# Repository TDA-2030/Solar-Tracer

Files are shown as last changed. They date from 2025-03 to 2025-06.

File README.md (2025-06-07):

# 太阳追踪器

## 参考

- https://www.pveducation.org/zh-hans/pvcdrom/%E9%98%B3%E5%85%89%E7%9A%84%E5%B1%9E%E6%80%A7/%E5%A4%AA%E9%98%B3%E7%9A%84%E9%AB%98%E7%B2%BE%E5%BA%A6%E5%AE%9A%E4%BD%8D
- http://106.37.81.211:8082/images/sjsimages/pdf/xw/xwB215_hebing/Y2177876.pdf
- https://jonacappelle.github.io/Master-Thesis/_madgwick_a_h_r_s_8c.html
- https://gml.noaa.gov/grad/solcalc/
- https://zh.planetcalc.com/318/

## 编译

esp-idf 版本：8497af9b77

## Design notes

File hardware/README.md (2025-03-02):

# Ferris Wheel

```
 ________                          __                 __       __ __                         __ 
|        \                        |  \               |  \  _  |  |  \                       |  \
| $$$$$$$______   ______   ______  \$$ _______       | $$ / \ | $| $$____   ______   ______ | $$
| $$__  /      \ /      \ /      \|  \/       \      | $$/  $\| $| $$    \ /      \ /      \| $$
| $$  \|  $$$$$$|  $$$$$$|  $$$$$$| $|  $$$$$$$      | $$  $$$\ $| $$$$$$$|  $$$$$$|  $$$$$$| $$
| $$$$$| $$    $| $$   \$| $$   \$| $$\$$    \       | $$ $$\$$\$| $$  | $| $$    $| $$    $| $$
| $$   | $$$$$$$| $$     | $$     | $$_\$$$$$$\      | $$$$  \$$$| $$  | $| $$$$$$$| $$$$$$$| $$
| $$    \$$     | $$     | $$     | $|       $$      | $$$    \$$| $$  | $$\$$     \\$$     | $$
 \$$     \$$$$$$$\$$      \$$      \$$\$$$$$$$        \$$      \$$\$$   \$$ \$$$$$$$ \$$$$$$$\$$
                                                                                                         
```

~ 一座点缀着繁星般灯光的旋转梦想摩天轮。🌟🎡 ~



## 使用说明

1. 插入电源，等待亮灯，在联网和不联网状态下都会在几秒后进入灯效循环播放，直到收到新的灯效指令。
2. 根据灯的颜色指示，判断当前状态
   1. 亮**红色**说明没有未配置网络，需要按照 `步骤 3` 进行配置
   2. 亮**紫色**说明已经配网，正在连接，只需等待连接完成变成**淡蓝色**即可

3. 配网步骤：
   1. 打开 RainMaker APP 
   2. 点击`添加设备`按钮
   3. 扫描下面的二维码   
   
4. 选择想要连接的 WiFi
5. 输入对应 WiFi 的密码
6. 点击`开始`按钮

## 硬件说明

- 供电输入：12V - 2A
- LED 灯数量：208 * 2
- 摩天轮坐舱数量：16
- 模型比例：1:100

## 灯颜色指示
1. 亮红色：未配网，等待配网
2. 亮紫色：正在联网
3. 亮蓝色：已联网，等待连接云端
4. 亮淡蓝色：已连接云端，可正常使用

## 重置设备方法

当你需要换一个 WiFi 连接或者不要联网的时候需要重置设备。

方法：插上电源等待亮灯一秒后拔掉电源，熄灭后再次插上电源，再次等待亮灯一秒后拔掉电源，如此**反复5次**后插上电源不再拔掉等待灯变成红色即重置成功。

## 编译固件的说明

下载 [ESP-IDF](https://github.com/espressif/esp-idf)，并安装好 ESP-IDF

> 库版本说明：
>
> esp-rainmaker: 7d506420d320a137bce6aaeb69a2059cc162efac
> esp-idf: 97bf63addecd1857a7017a29823a6c70fec99b04

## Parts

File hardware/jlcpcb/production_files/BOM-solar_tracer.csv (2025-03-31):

Comment | Designator | Footprint | LCSC
BMI270 | U3 | LGA-14_L3.0-W2.5-P0.50-BR | C2836813
QMC5883L | U4 | LGA-16_L3.0-W3.0-P0.50-BL_SQ | C976032
MountingHole_Pad | H4 | MountingHole_3.2mm_M3_Pad_Via
MountingHole_Pad | H1 | MountingHole_3.2mm_M3_Pad_Via
10uf | C10 | C_0603
10uf | C9 | C_0603
10uf | C7 | C_1206_3216Metric
10uf | C2 | C_0603
AT8236 | U6 | SOIC-8-1EP_3.9x4.9mm_P1.27mm_EP2.29x3mm
AT8236 | U5 | SOIC-8-1EP_3.9x4.9mm_P1.27mm_EP2.29x3mm
TX4137 | U2 | SOT-23-6
ESP32-S3-WROOM-1 | U1 | ESP32-S3-WROOM-1
0R | R15 | R_0402
0R | R14 | R_0402
4.7k | R13 | R_0402
4.7k | R12 | R_0402
NC | R11 | R_0402
NC | R10 | R_0402
1k | R9 | R_0402
10k | R8 | R_0402
10k | R7 | R_0402
100k | R6 | R_0402
33k | R5 | R_0402
200k | R4 | R_0402
4.7k | R3 | R_0402
4.7k | R2 | R_0402
10k | R1 | R_0402
22uH | L1 | L_Taiyo-Yuden_NR-40xx
MOTX | J7 | PinHeader_1x02_P2.54mm_Vertical
MOTX_ENCODER | J6 | PinHeader_1x04_P2.54mm_Vertical
MOTY | J5 | PinHeader_1x02_P2.54mm_Vertical
MOTY_ENCODER | J4 | PinHeader_1x04_P2.54mm_Vertical
POWER | J3 | PinHeader_1x02_P2.54mm_Vertical
GPS | J2 | PinHeader_1x04_P2.54mm_Vertical
DEBUG | J1 | PinHeader_1x06_P2.54mm_Vertical
MountingHole_Pad | H3 | MountingHole_3.2mm_M3_Pad_Via
MountingHole_Pad | H2 | MountingHole_3.2mm_M3_Pad_Via
RED | D5 | LED_0603
SMF5V0A | D4 | D_SMF
B5819W SL | D3 | D_SOD-123
RED | D2 | LED_0603
GREEN | D1 | LED_0603
10uf | C20 | C_0603
10uf | C19 | C_0603
100nf | C18 | C_0402
100nf | C17 | C_0402
4.7uf | C16 | C_0402
100nf | C15 | C_0402
220nf | C14 | C_0402
100nf | C13 | C_0402
100nf | C12 | C_0402
100n | C11 | C_0402
10uf | C8 | C_1206_3216Metric
10uf | C6 | C_1206_3216Metric
10uf | C5 | C_1206_3216Metric
100nf | C4 | C_0402
100nf | C3 | C_0402
100nf | C1 | C_0402

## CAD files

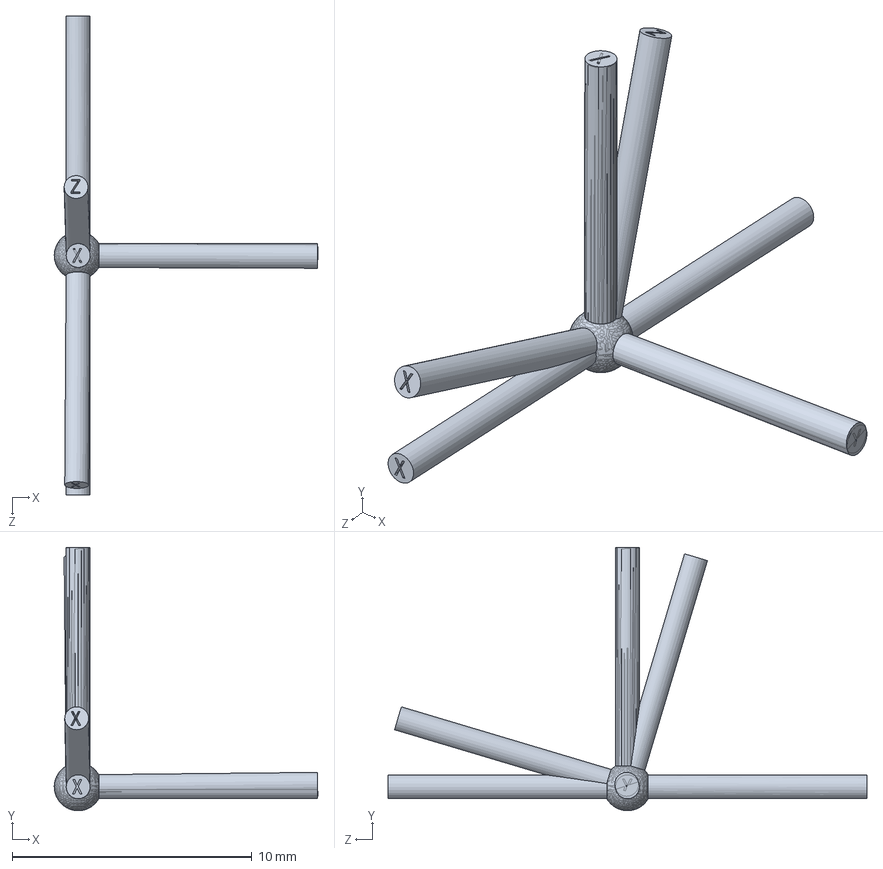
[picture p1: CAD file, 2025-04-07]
3d/坐标系.SLDASM
11.0 x 11.0 x 20.0 mm
坐标系 x 3

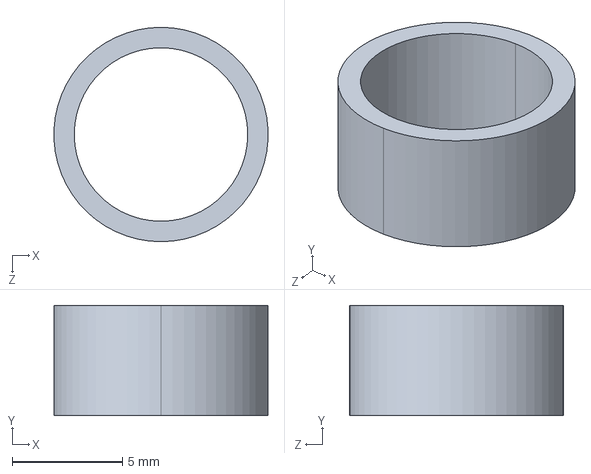
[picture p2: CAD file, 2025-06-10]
3d/轴套.STEP
9.69 x 5.00 x 9.70 mm

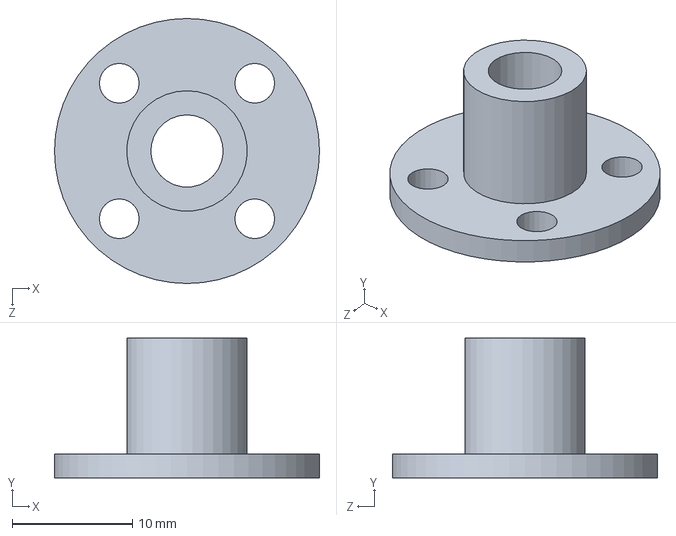
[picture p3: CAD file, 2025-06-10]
3d/法兰.SLDPRT
22.0 x 11.6 x 22.0 mm

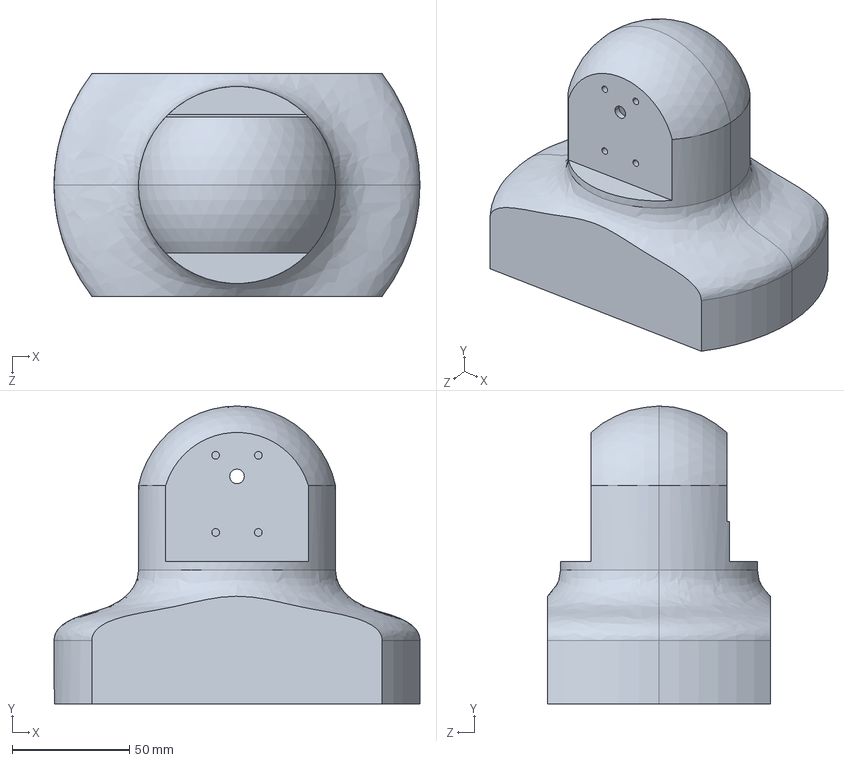
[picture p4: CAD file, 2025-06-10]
3d/上壳.STEP
156.0 x 127.0 x 95.0 mm

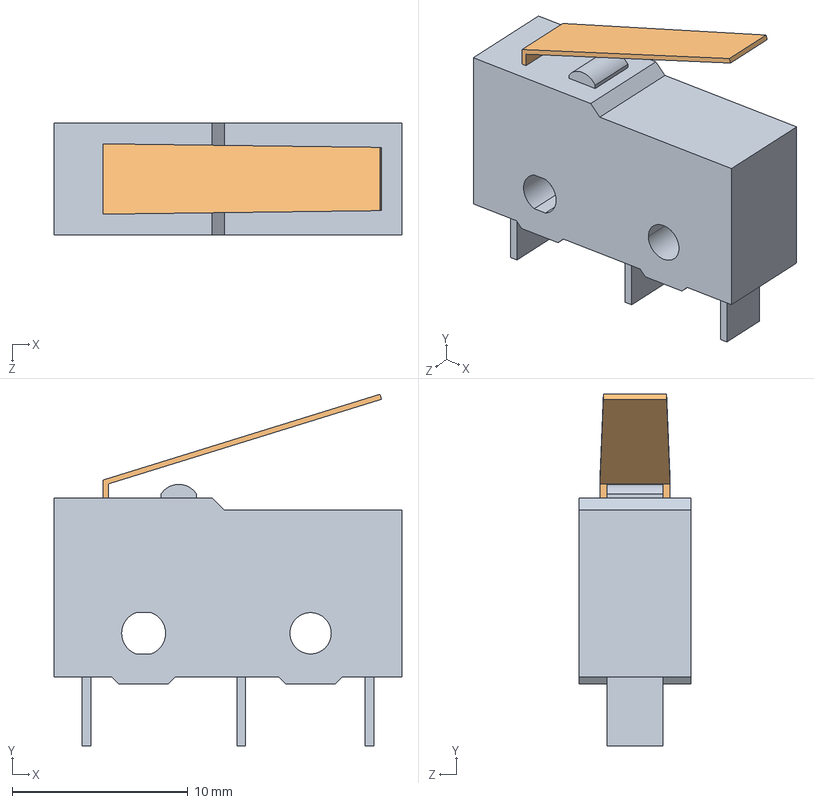
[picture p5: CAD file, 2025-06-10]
3d/SS_01GL_E.step
19.8 x 20.0 x 6.40 mm
SS_01GL_E_BASE
SS_01GL_E_ACTUATOR

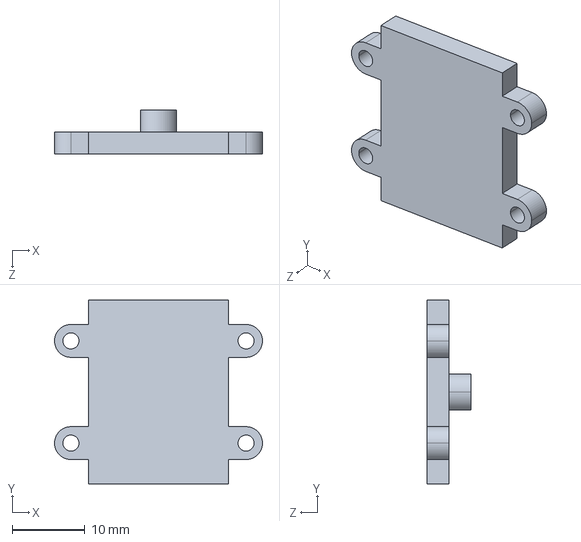
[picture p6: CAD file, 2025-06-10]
3d/imu盖板.STEP
28.5 x 25.2 x 6.00 mm

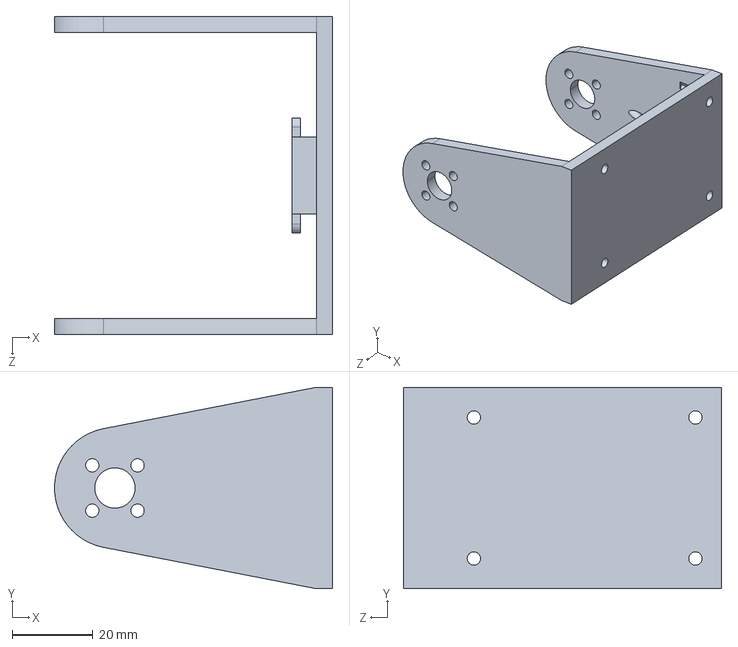
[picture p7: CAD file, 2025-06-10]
3d/U型板.STEP
69.0 x 50.0 x 79.0 mm

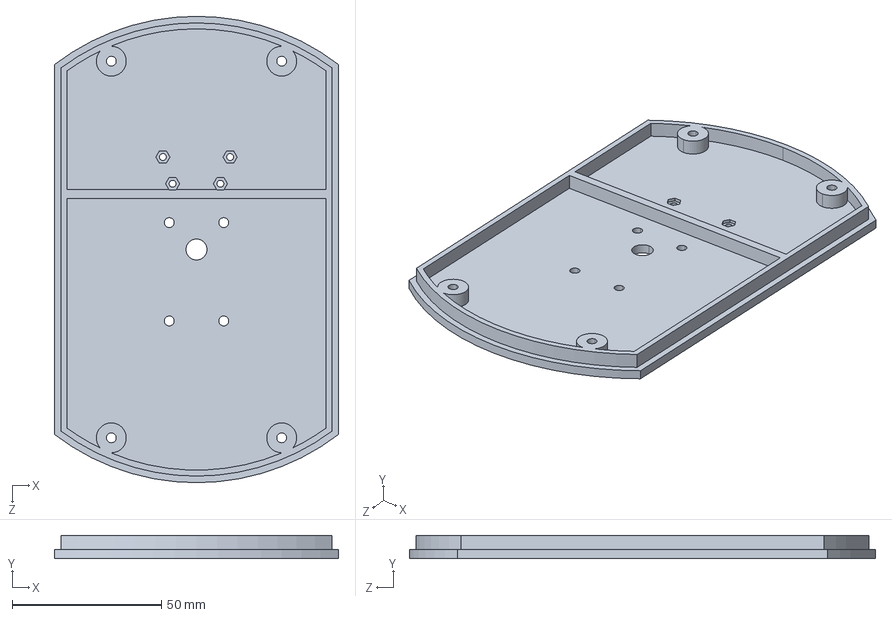
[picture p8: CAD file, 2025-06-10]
3d/底板.STEP
95.0 x 7.80 x 156.0 mm

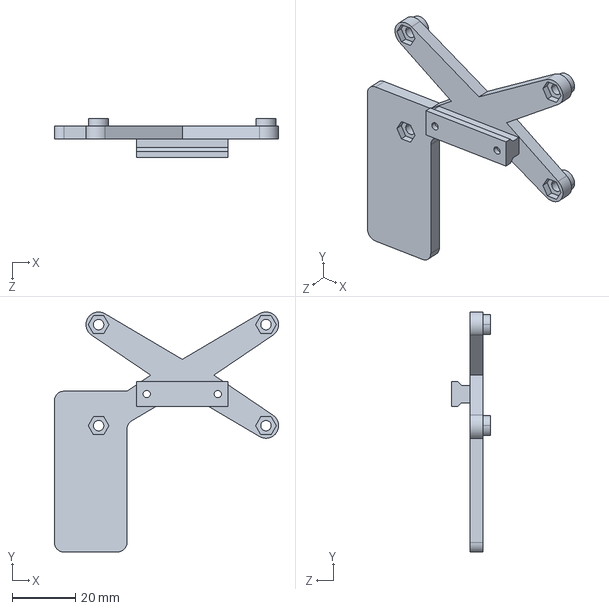
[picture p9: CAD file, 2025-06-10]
3d/pcb支架.STEP
71.0 x 76.0 x 12.5 mm

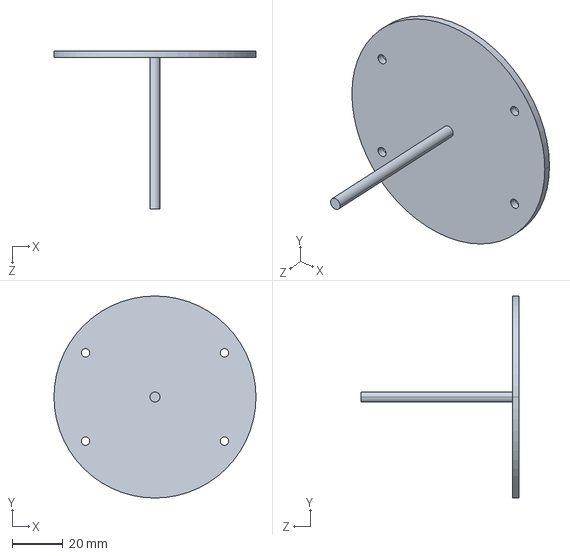
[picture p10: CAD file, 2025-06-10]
3d/太阳指向盘.STEP
80.0 x 80.0 x 62.5 mm

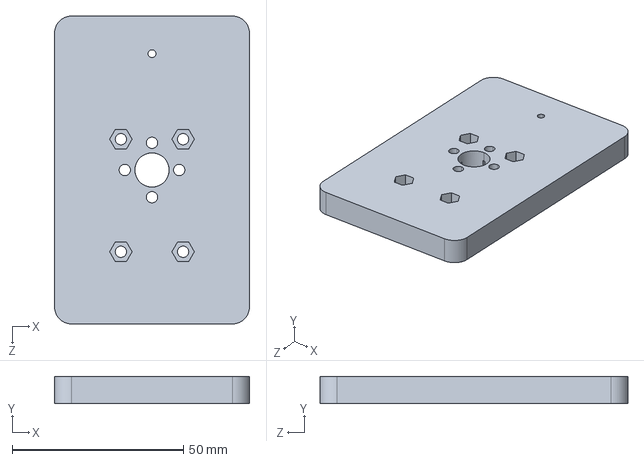
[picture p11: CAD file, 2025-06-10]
3d/底座.STEP
57.0 x 8.00 x 90.0 mm

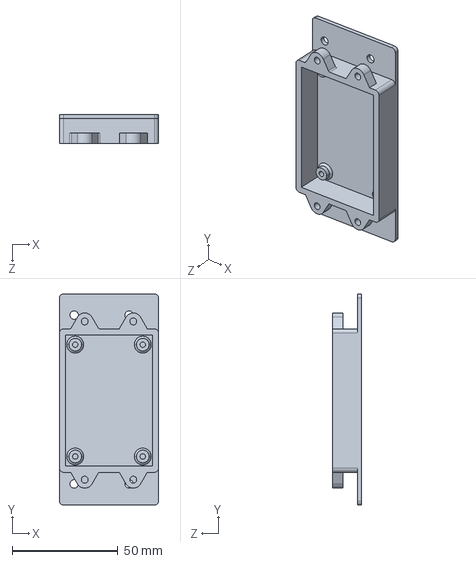
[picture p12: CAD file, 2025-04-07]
3d/imu固定板.STEP
47.0 x 100.0 x 13.8 mm

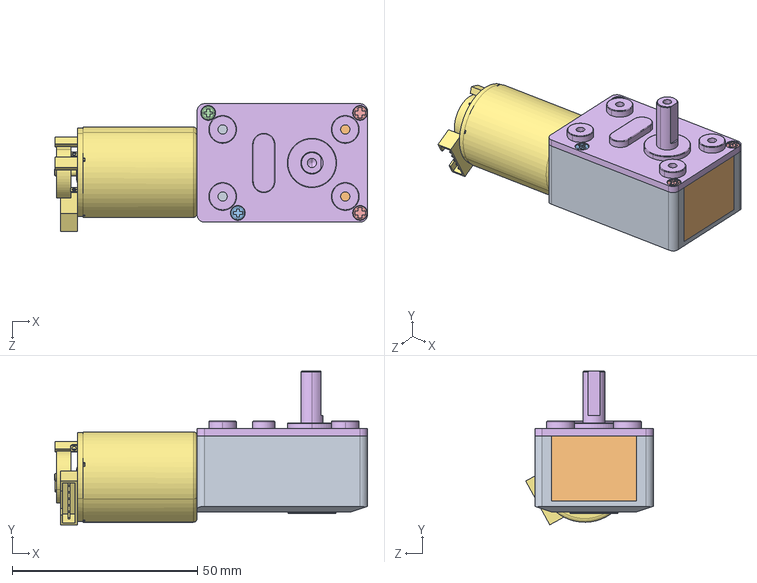
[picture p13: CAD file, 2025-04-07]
3d/2814300907JGY-370编码器.STEP
84.5 x 41.5 x 34.5 mm
JGY-370 -636
370晤鎢ん

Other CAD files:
3d/U型板.SLDPRT
3d/imu固定板.SLDPRT
3d/imu盖板.SLDPRT
3d/pcb支架.SLDPRT
3d/上壳.SLDPRT
3d/坐标系.SLDPRT
3d/太阳指向盘.SLDPRT
3d/底座.SLDPRT
3d/底板.SLDPRT
3d/轴套.SLDPRT

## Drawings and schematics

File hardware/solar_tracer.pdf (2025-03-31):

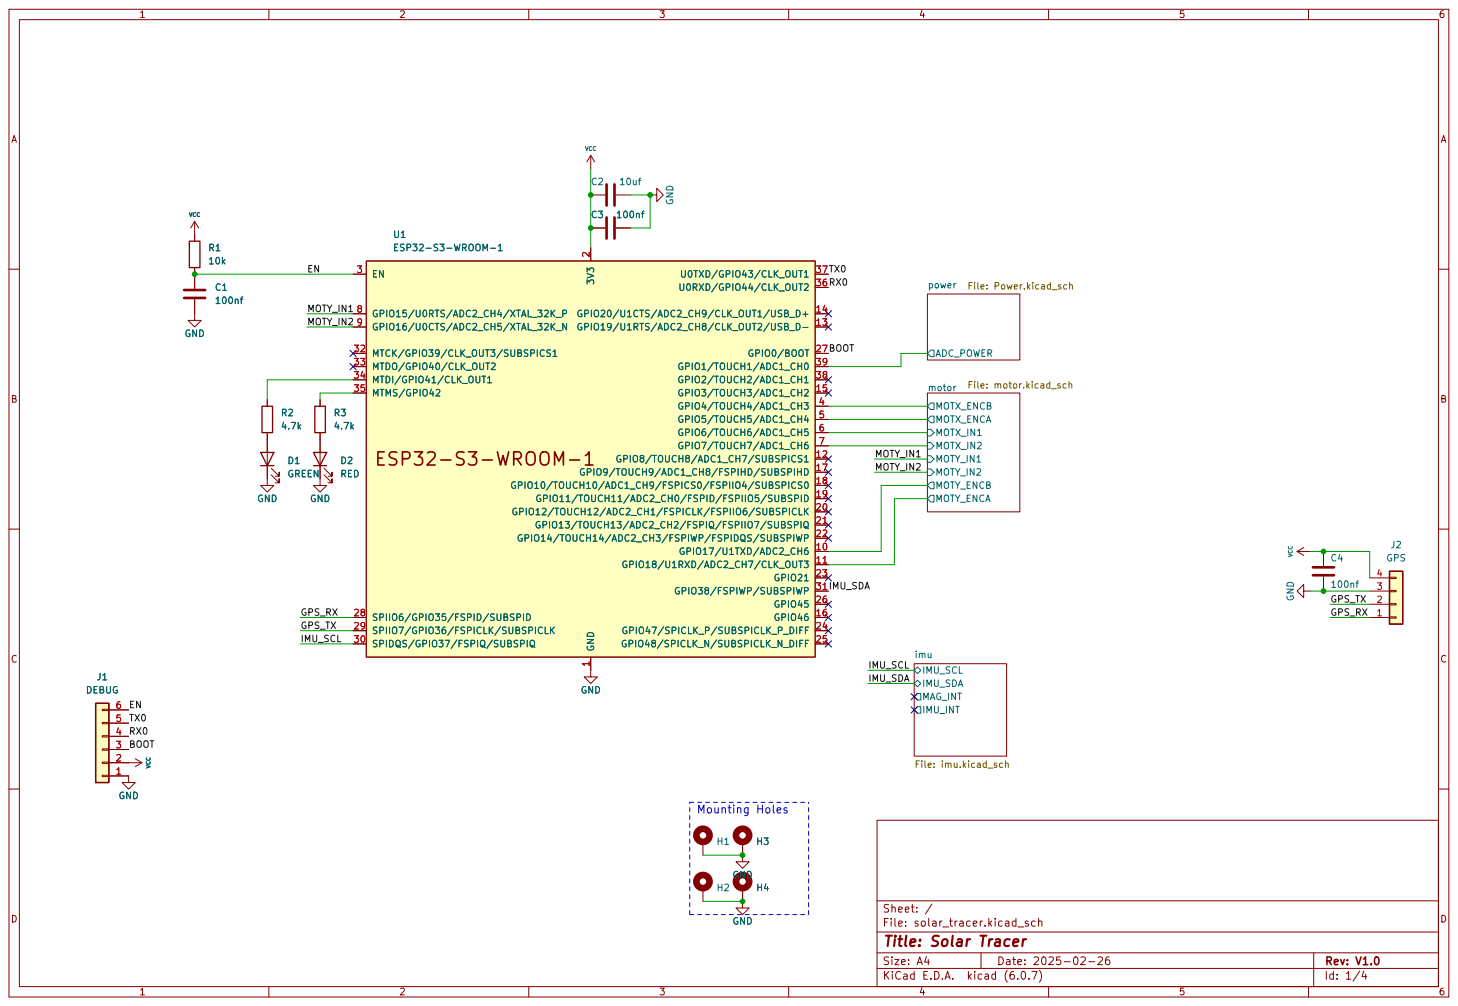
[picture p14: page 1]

2 GPIO12/TOUCH12/ADC2_CH1/FSPICLK/FSPIIO6/SUBSPICLK 20 GPIO13/TOUCH13/ADC2_CH2/FSPIQ/FSPIIO7/SUBSPIQ 21 GPIO14/TOUCH14/ADC2_CH3/FSPIWP/FSPIDQS/SUBSPIWP 22 GPIO21 23 GPIO47/SPICLK_P/SUBSPICLK_P_DIFF 24 GPIO48/SPICLK_N/SUBSPICLK_N_DIFF 25 GPIO45 26 GPIO0/BOOT 27 SPIIO6/GPIO35/FSPID/SUBSPID 28 SPIIO7/GPIO36/FSPICLK/SUBSPICLK 29 EN 3 SPIDQS/GPIO37/FSPIQ/SUBSPIQ 30 GPIO38/FSPIWP/SUBSPIWP 31 MTCK/GPIO39/CLK_OUT3/SUBSPICS1 32 MTDO/GPIO40/CLK_OUT2 33 MTDI/GPIO41/CLK_OUT1 34 MTMS/GPIO42 35 U0RXD/GPIO44/CLK_OUT2 36 U0TXD/GPIO43/CLK_OUT1 37 GPIO2/TOUCH2/ADC1_CH1 38 GPIO1/TOUCH1/ADC1_CH0 39 GPIO4/TOUCH4/ADC1_CH3 4 GPIO5/TOUCH5/ADC1_CH4 5 GPIO6/TOUCH6/ADC1_CH5 6 GPIO7/TOUCH7/ADC1_CH6 7 GPIO15/U0RTS/ADC2_CH4/XTAL_32K_P 8 GPIO16/U0CTS/ADC2_CH5/XTAL_32K_N 9 U1ESP32-S3-WROOM-1 H2

2 GPIO12/TOUCH12/ADC2_CH1/FSPICLK/FSPIIO6/SUBSPICLK 20 GPIO13/TOUCH13/ADC2_CH2/FSPIQ/FSPIIO7/SUBSPIQ 21 GPIO14/TOUCH14/ADC2_CH3/FSPIWP/FSPIDQS/SUBSPIWP 22 GPIO21 23 GPIO47/SPICLK_P/SUBSPICLK_P_DIFF 24 GPIO48/SPICLK_N/SUBSPICLK_N_DIFF 25 GPIO45 26 GPIO0/BOOT 27 SPIIO6/GPIO35/FSPID/SUBSPID 28 SPIIO7/GPIO36/FSPICLK/SUBSPICLK 29 EN 3 SPIDQS/GPIO37/FSPIQ/SUBSPIQ 30 GPIO38/FSPIWP/SUBSPIWP 31 MTCK/GPIO39/CLK_OUT3/SUBSPICS1 32 MTDO/GPIO40/CLK_OUT2 33 MTDI/GPIO41/CLK_OUT1 34 MTMS/GPIO42 35 U0RXD/GPIO44/CLK_OUT2 36 U0TXD/GPIO43/CLK_OUT1 37 GPIO2/TOUCH2/ADC1_CH1 38 GPIO1/TOUCH1/ADC1_CH0 39 GPIO4/TOUCH4/ADC1_CH3 4 GPIO5/TOUCH5/ADC1_CH4 5 GPIO6/TOUCH6/ADC1_CH5 6 GPIO7/TOUCH7/ADC1_CH6 7 GPIO15/U0RTS/ADC2_CH4/XTAL_32K_P 8 GPIO16/U0CTS/ADC2_CH5/XTAL_32K_N 9 GND GND

1 GPIO17/U1TXD/ADC2_CH6 10 GPIO18/U1RXD/ADC2_CH7/CLK_OUT3 11 GPIO8/TOUCH8/ADC1_CH7/SUBSPICS1 12 GPIO19/U1RTS/ADC2_CH8/CLK_OUT2/USB_D- 13 GPIO20/U1CTS/ADC2_CH9/CLK_OUT1/USB_D+ 14 GPIO3/TOUCH3/ADC1_CH2 15 GPIO46 16 GPIO9/TOUCH9/ADC1_CH8/FSPIHD/SUBSPIHD 17 GPIO10/TOUCH10/ADC1_CH9/FSPICS0/FSPIIO4/SUBSPICS0 18 GPIO11/TOUCH11/ADC2_CH0/FSPID/FSPIIO5/SUBSPID 19 3V3

Id: 1/4 Title: Solar Tracer

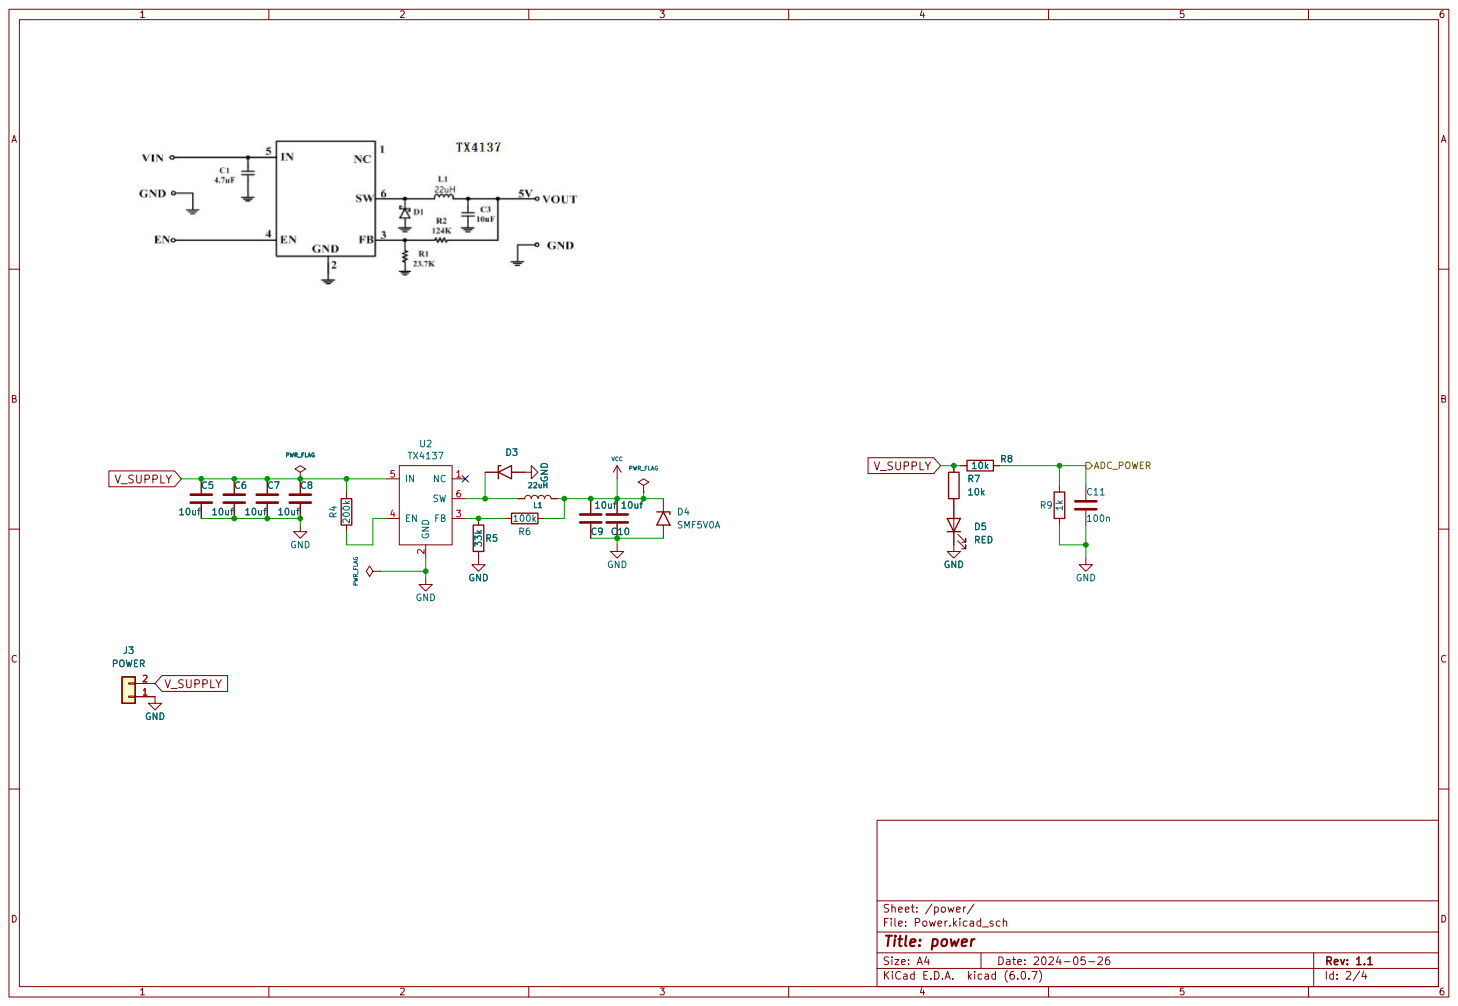
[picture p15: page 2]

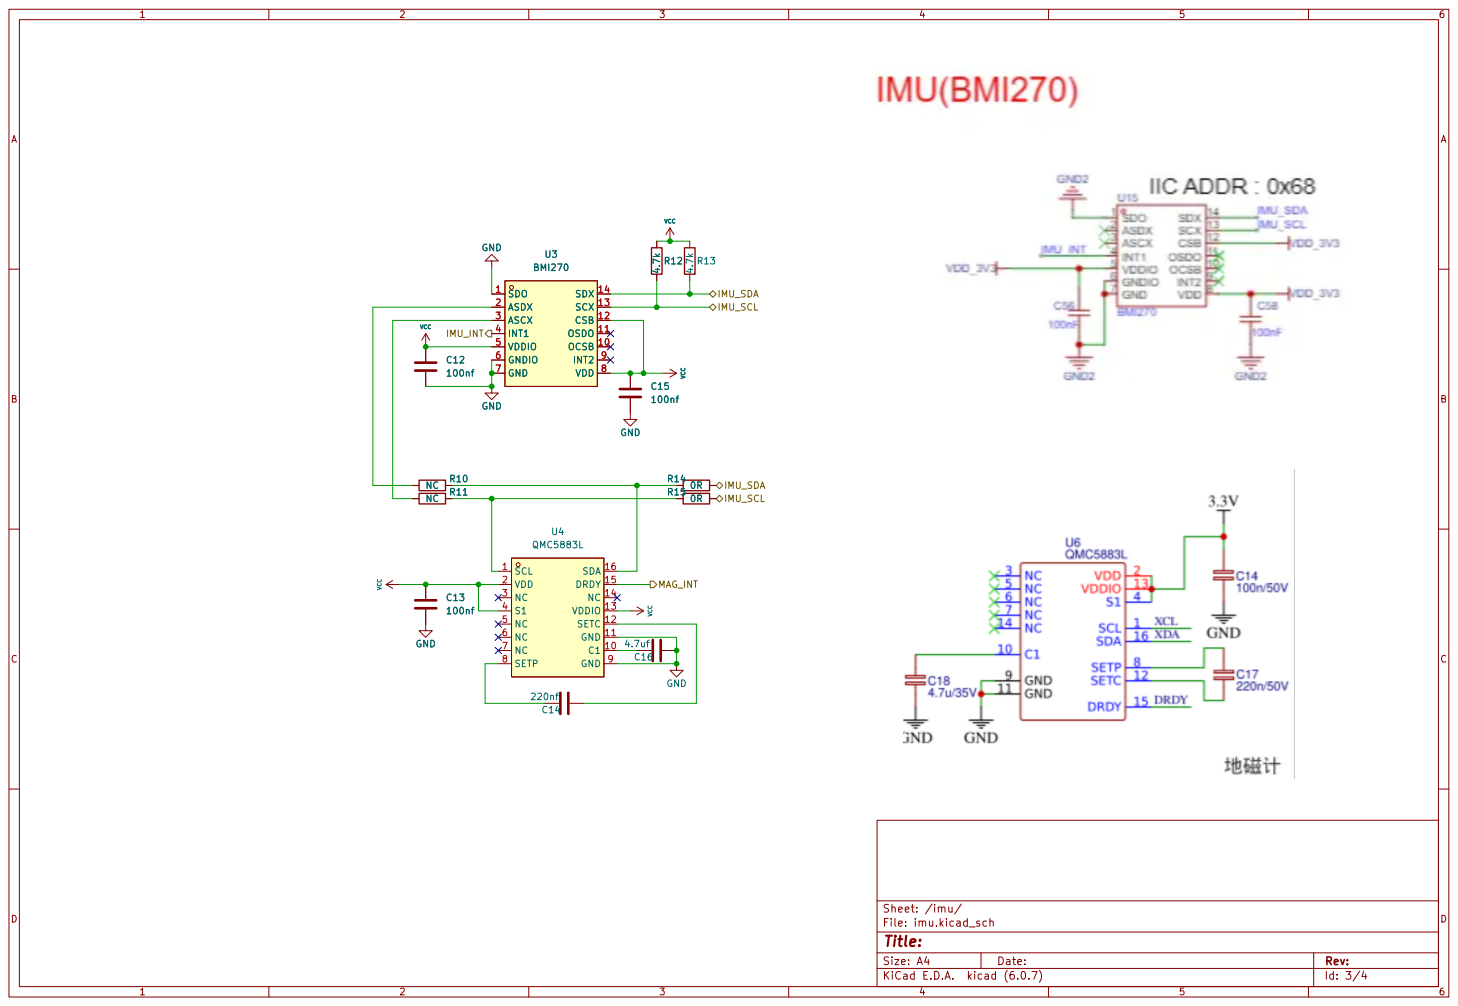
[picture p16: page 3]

File: imu.kicad_sch Sheet: /imu/
Id: 3/4 Title:

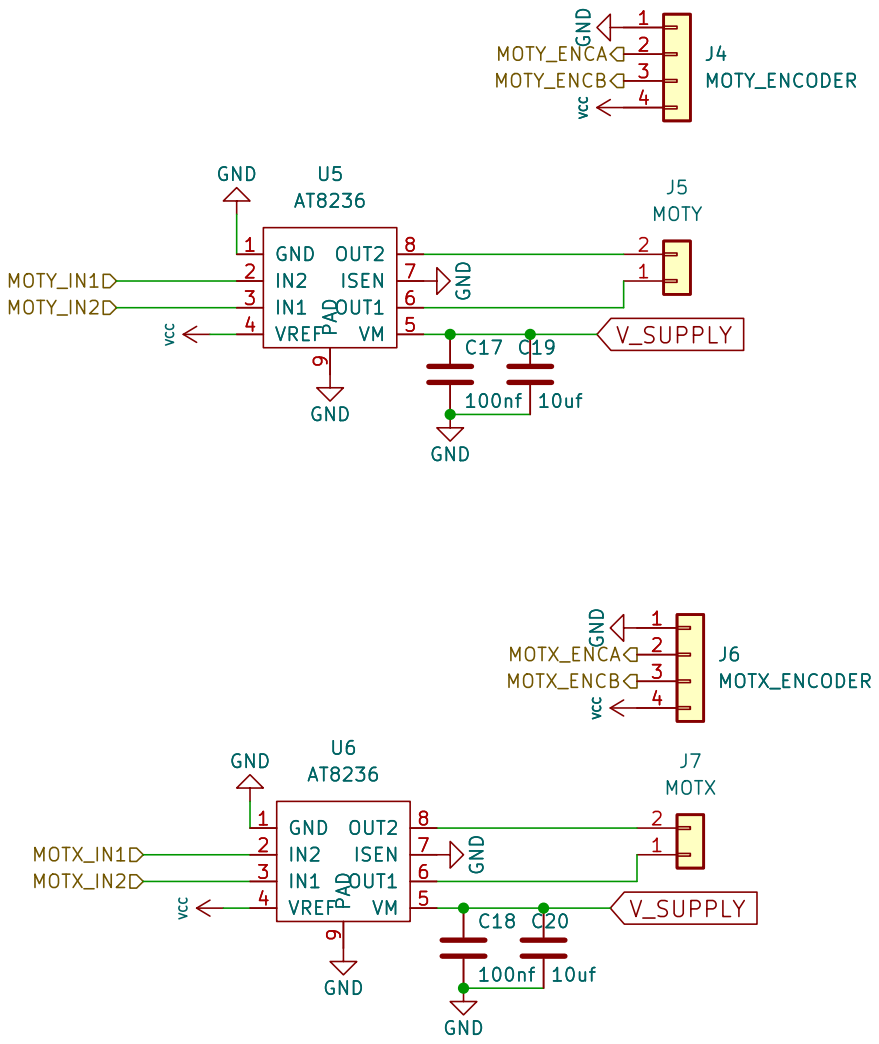
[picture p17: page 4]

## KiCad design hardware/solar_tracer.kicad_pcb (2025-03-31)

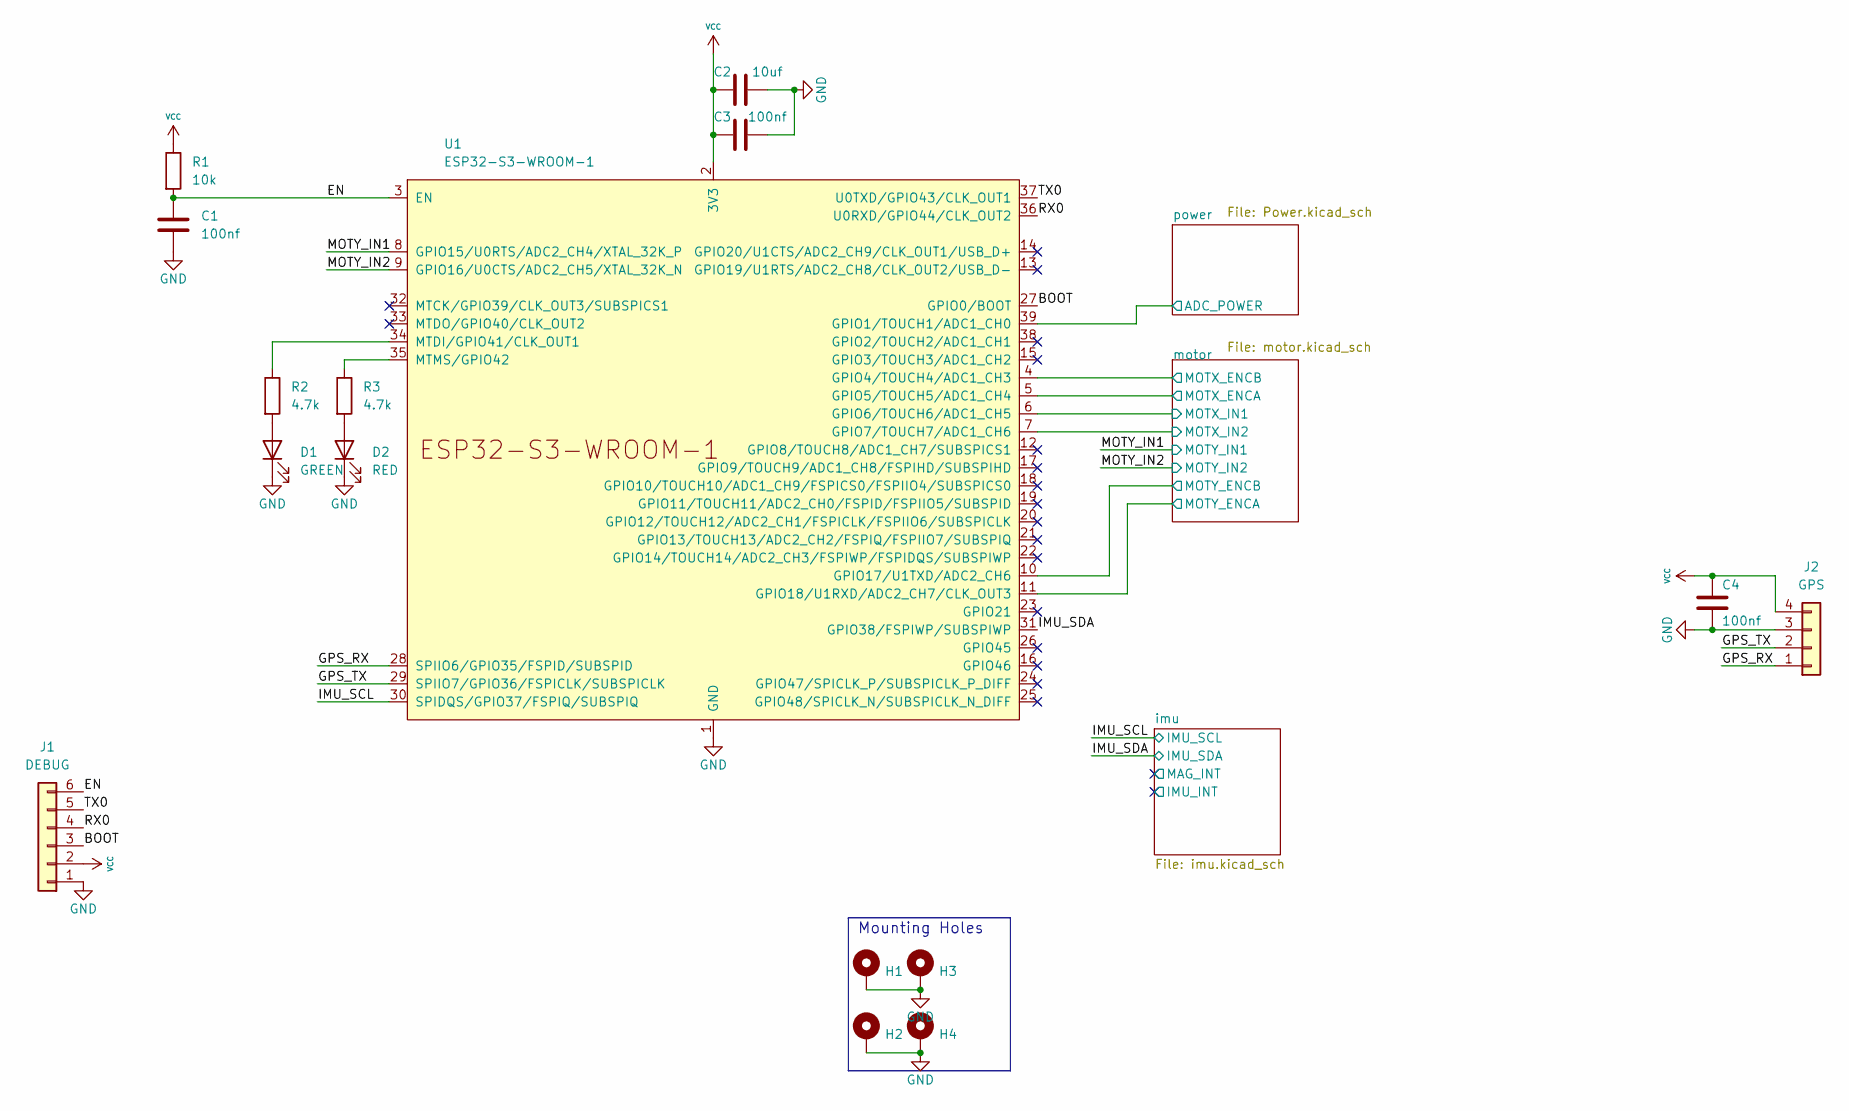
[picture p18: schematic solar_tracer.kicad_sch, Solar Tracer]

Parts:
C1, C3, C4: 100nf; C_0402_1005Metric
C2: 10uf; C_0603_1608Metric
D1: GREEN; LED_0603_1608Metric
D2: RED; LED_0603_1608Metric
H1, H2, H3, H4: MountingHole_Pad; MountingHole_3.2mm_M3_Pad_Via
J1: DEBUG; PinHeader_1x06_P2.54mm_Vertical
J2: GPS; PinHeader_1x04_P2.54mm_Vertical
R1: 10k; R_0402_1005Metric
R2, R3: 4.7k; R_0402_1005Metric
U1: ESP32-S3-WROOM-1

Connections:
/BOOT: J1.3, U1.27 (GPIO0/BOOT)
/EN: C1.1, J1.6, R1.2, U1.3 (EN)
/GPS_RX: J2.1, U1.28 (SPIIO6/GPIO35/FSPID/SUBSPID)
/GPS_TX: J2.2, U1.29 (SPIIO7/GPIO36/FSPICLK/SUBSPICLK)
/IMU_SCL: U1.30 (SPIDQS/GPIO37/FSPIQ/SUBSPIQ); also elsewhere on the board
/IMU_SDA: U1.31 (GPIO38/FSPIWP/SUBSPIWP); also elsewhere on the board
/MOTY_IN1: U1.8 (GPIO15/U0RTS/ADC2_CH4/XTAL_32K_P); also elsewhere on the board
/MOTY_IN2: U1.9 (GPIO16/U0CTS/ADC2_CH5/XTAL_32K_N); also elsewhere on the board
/RX0: J1.4, U1.36 (U0RXD/GPIO44/CLK_OUT2)
/TX0: J1.5, U1.37 (U0TXD/GPIO43/CLK_OUT1)
/motor/MOTX_ENCA: U1.5 (GPIO5/TOUCH5/ADC1_CH4); also elsewhere on the board
/motor/MOTX_ENCB: U1.4 (GPIO4/TOUCH4/ADC1_CH3); also elsewhere on the board
/motor/MOTX_IN1: U1.6 (GPIO6/TOUCH6/ADC1_CH5); also elsewhere on the board
/motor/MOTX_IN2: U1.7 (GPIO7/TOUCH7/ADC1_CH6); also elsewhere on the board
/motor/MOTY_ENCA: U1.11 (GPIO18/U1RXD/ADC2_CH7/CLK_OUT3); also elsewhere on the board
/motor/MOTY_ENCB: U1.10 (GPIO17/U1TXD/ADC2_CH6); also elsewhere on the board
/power/ADC_POWER: U1.39 (GPIO1/TOUCH1/ADC1_CH0); also elsewhere on the board
GND: C1.2, C2.2, C3.2, C4.2, D1.1 (K), D2.1 (K), H1.1, H2.1, H3.1, H4.1, J1.1, J2.3, U1.1 (GND), U1.40 (GND), U1.41 (GND); also elsewhere on the board
unnamed: D1.2 (A), R2.2
unnamed: D2.2 (A), R3.2
unnamed: R2.1, U1.34 (MTDI/GPIO41/CLK_OUT1)
unnamed: R3.1, U1.35 (MTMS/GPIO42)
VCC: C2.1, C3.1, C4.1, J1.2, J2.4, R1.1, U1.2 (3V3); also elsewhere on the board

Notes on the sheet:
Mounting Holes

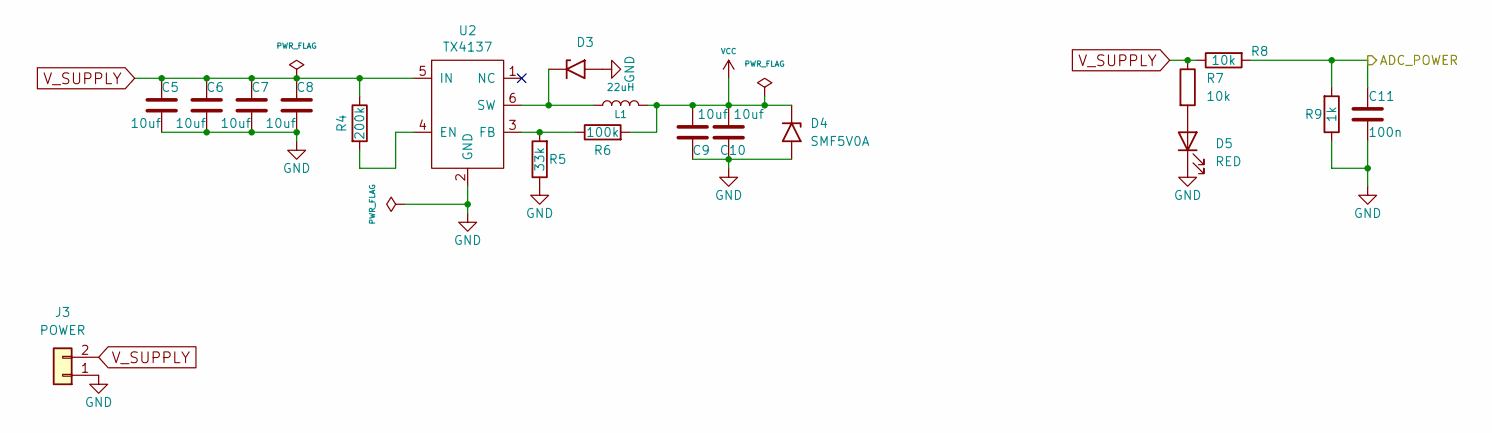
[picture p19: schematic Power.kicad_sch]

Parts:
C5, C6, C7, C8: 10uf; C_1206_3216Metric
C9, C10: 10uf; C_0603_1608Metric
C11: 100n; C_0402_1005Metric
D3: B5819W SL; D_SOD-123
D4: SMF5V0A; D_SMF
D5: RED; LED_0603_1608Metric
J3: POWER; PinHeader_1x02_P2.54mm_Vertical
L1: 22uH; L_Taiyo-Yuden_NR-40xx
R4: 200k; R_0402_1005Metric
R5: 33k; R_0402_1005Metric
R6: 100k; R_0402_1005Metric
R7, R8: 10k; R_0402_1005Metric
R9: 1k; R_0402_1005Metric
U2: TX4137; SOT-23-6

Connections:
/power/ADC_POWER: C11.2, R8.2, R9.2; also elsewhere on the board
GND: C5.1, C6.1, C7.1, C8.1, C9.1, C10.1, C11.1, D3.2 (A2), D4.2 (A2), D5.1 (K), J3.1, R5.1, R9.1, U2.2 (GND); also elsewhere on the board
unnamed: D3.1 (A1), L1.1, U2.6 (SW)
unnamed: D5.2 (A), R7.2
unnamed: R4.2, U2.4 (EN)
unnamed: R5.2, R6.1, U2.3 (FB)
VCC: C9.2, C10.2, D4.1 (A1), L1.2, R6.2; also elsewhere on the board
V_SUPPLY: C5.2, C6.2, C7.2, C8.2, J3.2, R4.1, R7.1, R8.1, U2.5 (IN); also elsewhere on the board

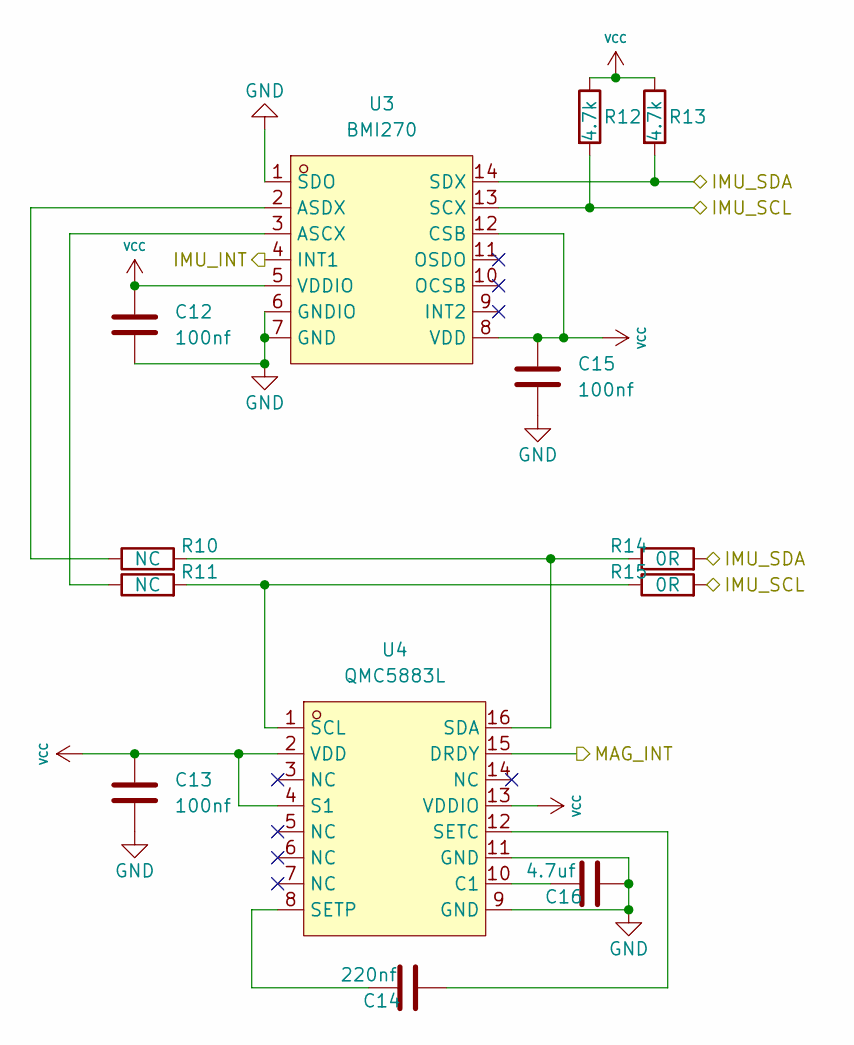
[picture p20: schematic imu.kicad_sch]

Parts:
C12, C13, C15: 100nf; C_0402_1005Metric
C14: 220nf; C_0402_1005Metric
C16: 4.7uf; C_0402_1005Metric
R10, R11: NC; R_0402_1005Metric
R12, R13: 4.7k; R_0402_1005Metric
R14, R15: 0R; R_0402_1005Metric
U3: BMI270; LGA-14_L3.0-W2.5-P0.50-BR; LCSC Part C2836813
U4: QMC5883L; LGA-16_L3.0-W3.0-P0.50-BL_SQ; LCSC Part C976032

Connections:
/IMU_SCL: R12.2, R15.2, U3.13 (SCX); also elsewhere on the board
/IMU_SDA: R13.2, R14.2, U3.14 (SDX); also elsewhere on the board
/imu/IMU_INT: U3.4 (INT1)
/imu/MAG_INT: U4.15 (DRDY)
GND: C12.1, C13.1, C15.1, C16.1, U3.1 (SDO), U3.6 (GNDIO), U3.7 (GND), U4.9 (GND), U4.11 (GND); also elsewhere on the board
unnamed: C14.1, U4.12 (SETC)
unnamed: C14.2, U4.8 (SETP)
unnamed: C16.2, U4.10 (C1)
unnamed: R10.1, U3.2 (ASDX)
unnamed: R10.2, R14.1, U4.16 (SDA)
unnamed: R11.1, U3.3 (ASCX)
unnamed: R11.2, R15.1, U4.1 (SCL)
VCC: C12.2, C13.2, C15.2, R12.1, R13.1, U3.5 (VDDIO), U3.8 (VDD), U3.12 (CSB), U4.2 (VDD), U4.4 (S1), U4.13 (VDDIO); also elsewhere on the board

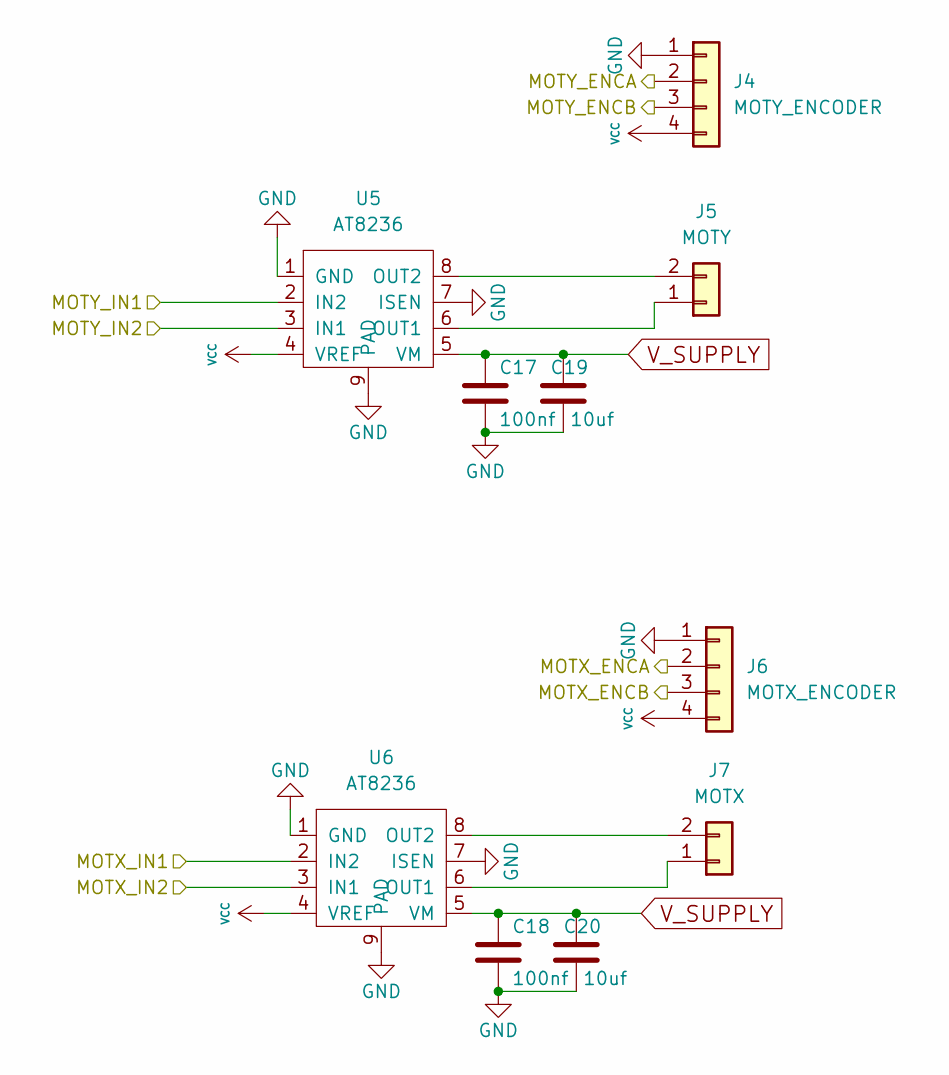
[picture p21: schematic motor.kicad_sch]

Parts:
C17, C18: 100nf; C_0402_1005Metric
C19, C20: 10uf; C_0603_1608Metric
J4: MOTY_ENCODER; PinHeader_1x04_P2.54mm_Vertical
J5: MOTY; PinHeader_1x02_P2.54mm_Vertical
J6: MOTX_ENCODER; PinHeader_1x04_P2.54mm_Vertical
J7: MOTX; PinHeader_1x02_P2.54mm_Vertical
U5, U6: AT8236; SOIC-8-1EP_3.9x4.9mm_P1.27mm_EP2.29x3mm

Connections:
/MOTY_IN1: U5.2 (IN2); also elsewhere on the board
/MOTY_IN2: U5.3 (IN1); also elsewhere on the board
/motor/MOTX_ENCA: J6.2; also elsewhere on the board
/motor/MOTX_ENCB: J6.3; also elsewhere on the board
/motor/MOTX_IN1: U6.2 (IN2); also elsewhere on the board
/motor/MOTX_IN2: U6.3 (IN1); also elsewhere on the board
/motor/MOTY_ENCA: J4.2; also elsewhere on the board
/motor/MOTY_ENCB: J4.3; also elsewhere on the board
GND: C17.2, C18.2, C19.1, C20.1, J4.1, J6.1, U5.1 (GND), U5.7 (ISEN), U5.9 (PAD), U6.1 (GND), U6.7 (ISEN), U6.9 (PAD); also elsewhere on the board
unnamed: J5.1, U5.6 (OUT1)
unnamed: J5.2, U5.8 (OUT2)
unnamed: J7.1, U6.6 (OUT1)
unnamed: J7.2, U6.8 (OUT2)
VCC: J4.4, J6.4, U5.4 (VREF), U6.4 (VREF); also elsewhere on the board
V_SUPPLY: C17.1, C18.1, C19.2, C20.2, U5.5 (VM), U6.5 (VM); also elsewhere on the board

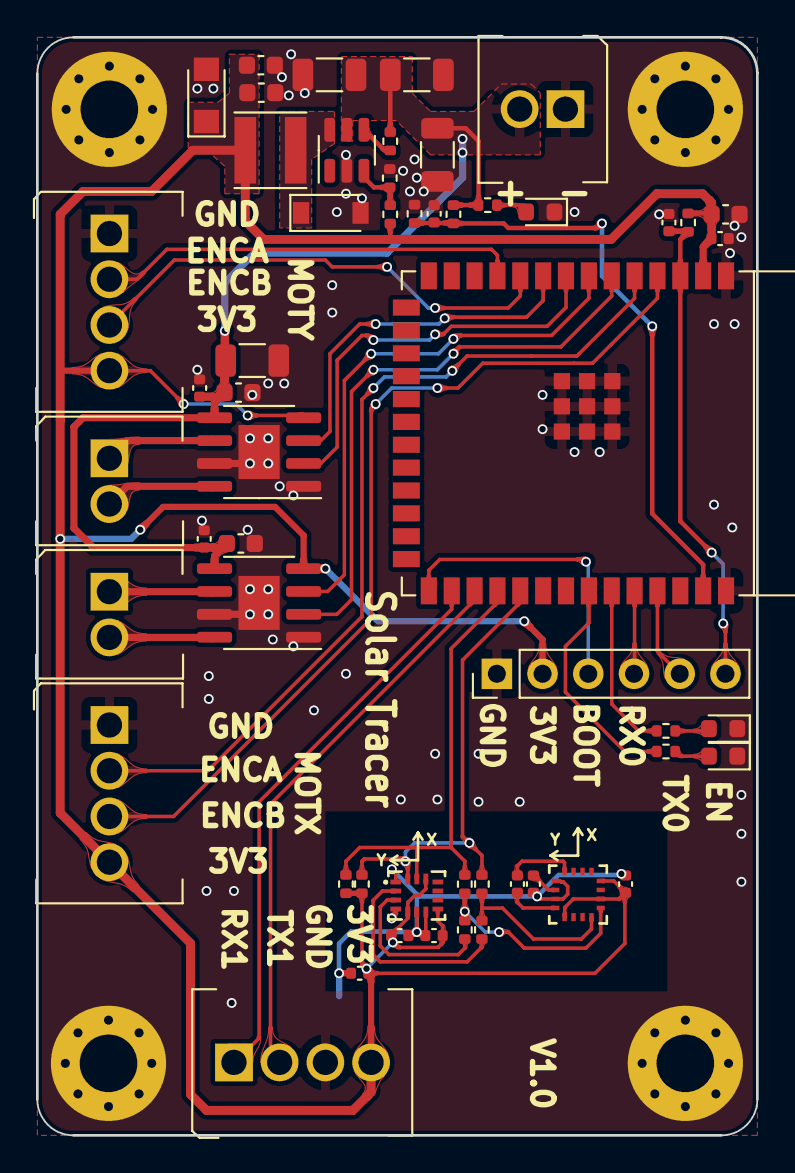
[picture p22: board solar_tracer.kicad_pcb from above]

Board: 2 copper layers, 40.0 x 61.0 mm, 58 parts (0 on the bottom side), 39 nets.

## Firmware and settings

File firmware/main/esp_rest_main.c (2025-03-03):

/* HTTP Restful API Server Example

   This example code is in the Public Domain (or CC0 licensed, at your option.)

   Unless required by applicable law or agreed to in writing, this
   software is distributed on an "AS IS" BASIS, WITHOUT WARRANTIES OR
   CONDITIONS OF ANY KIND, either express or implied.
*/
#include "sdkconfig.h"
#include "driver/gpio.h"
#include "esp_vfs_semihost.h"
#include "esp_vfs_fat.h"
#include "esp_spiffs.h"
#include "sdmmc_cmd.h"
#include "nvs_flash.h"
#include "esp_netif.h"
#include "esp_event.h"
#include "esp_log.h"
#include "mdns.h"
#include "lwip/apps/netbiosns.h"
#include "lwip/inet.h"
#include "esp_mac.h"
#include "esp_wifi.h"
#if CONFIG_EXAMPLE_WEB_DEPLOY_SD
#include "driver/sdmmc_host.h"
#endif

#define MDNS_INSTANCE "esp home web server"

static const char *TAG = "web";

esp_err_t start_rest_server(const char *base_path);

static void initialise_mdns(void)
{
    mdns_init();
    mdns_hostname_set(CONFIG_EXAMPLE_MDNS_HOST_NAME);
    mdns_instance_name_set(MDNS_INSTANCE);

    mdns_txt_item_t serviceTxtData[] = {
        {"board", "esp32"},
        {"path", "/"}
    };

    ESP_ERROR_CHECK(mdns_service_add("ESP32-WebServer", "_http", "_tcp", 80, serviceTxtData,
                                     sizeof(serviceTxtData) / sizeof(serviceTxtData[0])));
}

#if CONFIG_EXAMPLE_WEB_DEPLOY_SEMIHOST
esp_err_t init_fs(void)
{
    esp_err_t ret = esp_vfs_semihost_register(CONFIG_EXAMPLE_WEB_MOUNT_POINT);
    if (ret != ESP_OK) {
        ESP_LOGE(TAG, "Failed to register semihost driver (%s)!", esp_err_to_name(ret));
        return ESP_FAIL;
    }
    return ESP_OK;
}
#endif

#if CONFIG_EXAMPLE_WEB_DEPLOY_SD
esp_err_t init_fs(void)
{
    sdmmc_host_t host = SDMMC_HOST_DEFAULT();
    sdmmc_slot_config_t slot_config = SDMMC_SLOT_CONFIG_DEFAULT();

    gpio_set_pull_mode(15, GPIO_PULLUP_ONLY); // CMD
    gpio_set_pull_mode(2, GPIO_PULLUP_ONLY);  // D0
    gpio_set_pull_mode(4, GPIO_PULLUP_ONLY);  // D1
    gpio_set_pull_mode(12, GPIO_PULLUP_ONLY); // D2
    gpio_set_pull_mode(13, GPIO_PULLUP_ONLY); // D3

    esp_vfs_fat_sdmmc_mount_config_t mount_config = {
        .format_if_mount_failed = true,
        .max_files = 4,
        .allocation_unit_size = 16 * 1024
    };

    sdmmc_card_t *card;
    esp_err_t ret = esp_vfs_fat_sdmmc_mount(CONFIG_EXAMPLE_WEB_MOUNT_POINT, &host, &slot_config, &mount_config, &card);
    if (ret != ESP_OK) {
        if (ret == ESP_FAIL) {
            ESP_LOGE(TAG, "Failed to mount filesystem.");
        } else {
            ESP_LOGE(TAG, "Failed to initialize the card (%s)", esp_err_to_name(ret));
        }
        return ESP_FAIL;
    }
    /* print card info if mount successfully */
    sdmmc_card_print_info(stdout, card);
    return ESP_OK;
}
#endif

#if CONFIG_EXAMPLE_WEB_DEPLOY_SF
esp_err_t init_fs(void)
{
    esp_vfs_spiffs_conf_t conf = {
        .base_path = CONFIG_EXAMPLE_WEB_MOUNT_POINT,
        .partition_label = NULL,
        .max_files = 5,
        .format_if_mount_failed = false
    };
    esp_err_t ret = esp_vfs_spiffs_register(&conf);

    if (ret != ESP_OK) {
        if (ret == ESP_FAIL) {
            ESP_LOGE(TAG, "Failed to mount or format filesystem");
        } else if (ret == ESP_ERR_NOT_FOUND) {
            ESP_LOGE(TAG, "Failed to find SPIFFS partition");
        } else {
            ESP_LOGE(TAG, "Failed to initialize SPIFFS (%s)", esp_err_to_name(ret));
        }
        return ESP_FAIL;
    }

    size_t total = 0, used = 0;
    ret = esp_spiffs_info(NULL, &total, &used);
    if (ret != ESP_OK) {
        ESP_LOGE(TAG, "Failed to get SPIFFS partition information (%s)", esp_err_to_name(ret));
    } else {
        ESP_LOGI(TAG, "Partition size: total: %d, used: %d", total, used);
    }
    return ESP_OK;
}
#endif

#define EXAMPLE_ESP_WIFI_SSID "ESP32"
#define EXAMPLE_ESP_WIFI_PASS ""

static void wifi_event_handler(void *arg, esp_event_base_t event_base,
                               int32_t event_id, void *event_data)
{
    if (event_id == WIFI_EVENT_AP_STACONNECTED) {
        wifi_event_ap_staconnected_t *event = (wifi_event_ap_staconnected_t *)event_data;
        ESP_LOGI(TAG, "station " MACSTR " join, AID=%d",
                 MAC2STR(event->mac), event->aid);
    } else if (event_id == WIFI_EVENT_AP_STADISCONNECTED) {
        wifi_event_ap_stadisconnected_t *event = (wifi_event_ap_stadisconnected_t *)event_data;
        ESP_LOGI(TAG, "station " MACSTR " leave, AID=%d, reason=%d",
                 MAC2STR(event->mac), event->aid, event->reason);
    }
}

static void wifi_init_softap(void)
{
    wifi_init_config_t cfg = WIFI_INIT_CONFIG_DEFAULT();
    ESP_ERROR_CHECK(esp_wifi_init(&cfg));

    ESP_ERROR_CHECK(esp_event_handler_register(WIFI_EVENT, ESP_EVENT_ANY_ID, &wifi_event_handler, NULL));

    wifi_config_t wifi_config = {
        .ap = {
            .ssid = EXAMPLE_ESP_WIFI_SSID,
            .ssid_len = strlen(EXAMPLE_ESP_WIFI_SSID),
            .password = EXAMPLE_ESP_WIFI_PASS,
            .max_connection = 2,
            .authmode = WIFI_AUTH_WPA_WPA2_PSK
        },
    };
    if (strlen(EXAMPLE_ESP_WIFI_PASS) == 0) {
        wifi_config.ap.authmode = WIFI_AUTH_OPEN;
    }

    ESP_ERROR_CHECK(esp_wifi_set_mode(WIFI_MODE_AP));
    ESP_ERROR_CHECK(esp_wifi_set_config(ESP_IF_WIFI_AP, &wifi_config));
    ESP_ERROR_CHECK(esp_wifi_start());

    esp_netif_ip_info_t ip_info;
    esp_netif_get_ip_info(esp_netif_get_handle_from_ifkey("WIFI_AP_DEF"), &ip_info);

    char ip_addr[16];
    inet_ntoa_r(ip_info.ip.addr, ip_addr, 16);
    ESP_LOGI(TAG, "Set up softAP with IP: %s", ip_addr);

    ESP_LOGI(TAG, "wifi_init_softap finished. SSID:'%s' password:'%s'",
             EXAMPLE_ESP_WIFI_SSID, EXAMPLE_ESP_WIFI_PASS);
}


void start_web(void)
{
    ESP_ERROR_CHECK(esp_netif_init());
    ESP_ERROR_CHECK(esp_event_loop_create_default());
    initialise_mdns();
    netbiosns_init();
    netbiosns_set_name(CONFIG_EXAMPLE_MDNS_HOST_NAME);

    esp_netif_create_default_wifi_ap();
    wifi_init_softap();

    // ESP_ERROR_CHECK(example_connect());
    ESP_ERROR_CHECK(init_fs());
    ESP_ERROR_CHECK(start_rest_server(CONFIG_EXAMPLE_WEB_MOUNT_POINT));
}

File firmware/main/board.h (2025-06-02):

/*

  */
#ifndef __BOARD_H_
#define __BOARD_H_

#include "i2c_bus.h"


#ifdef __cplusplus
extern "C" {
#endif

#define BOARD_IO_MOTY_IN1 15
#define BOARD_IO_MOTY_IN2 16
#define BOARD_IO_MOTY_ENC_A 17
#define BOARD_IO_MOTY_ENC_B 18


#define BOARD_IO_MOTX_IN1 6
#define BOARD_IO_MOTX_IN2 7
#define BOARD_IO_MOTX_ENC_A 5
#define BOARD_IO_MOTX_ENC_B 4


#define BOARD_IO_GPS_RX 35
#define BOARD_IO_GPS_TX 36

#define BOARD_IO_IMU_SDA 38
#define BOARD_IO_IMU_SCL 37

#define BOARD_IO_LED_RED 42
#define BOARD_IO_LED_GREEN 41


esp_err_t bsp_i2c_init(void);
i2c_bus_handle_t bsp_i2c_get_handle(int index);


#ifdef __cplusplus
}
#endif

#endif

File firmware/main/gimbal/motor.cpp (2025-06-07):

/* LEDC (LED Controller) basic example

   This example code is in the Public Domain (or CC0 licensed, at your option.)

   Unless required by applicable law or agreed to in writing, this
   software is distributed on an "AS IS" BASIS, WITHOUT WARRANTIES OR
   CONDITIONS OF ANY KIND, either express or implied.
*/
#include <stdio.h>
#include <math.h>
#include "freertos/FreeRTOS.h"
#include "freertos/task.h"
#include "freertos/timers.h"
#include "driver/ledc.h"
#include "esp_timer.h"
#include "esp_err.h"
#include "esp_log.h"
#include "board.h"
#include "motor.h"
#include "pid.h"
#include "led.h"

static const char *TAG = "motor";



#define STALL_SPEED_THRESHOLD   0.1f    // Speed threshold for stall detection
#define RECOVERY_OUTPUT_RATIO   0.8f    // Output ratio threshold for recovery


const char* Motor::motStateDescriptions[] = {
#define X(name, desc) desc,
    MOT_STATE_LIST
#undef X
};

bool EncoderSensor::init(int gpio_enca, int gpio_encb, float cpr)
{
    ESP_LOGI(TAG, "install pcnt unit");
    pcnt_unit_config_t unit_config = {
        .low_limit = -3000,
        .high_limit = 3000,
        .intr_priority = 0,
        .flags = {
            .accum_count = true,
        }
    };
    ESP_ERROR_CHECK(pcnt_new_unit(&unit_config, &pcnt_unit));

    pcnt_glitch_filter_config_t filter_config = {
        .max_glitch_ns = 1000,
    };
    ESP_ERROR_CHECK(pcnt_unit_set_glitch_filter(pcnt_unit, &filter_config));

    ESP_LOGI(TAG, "install pcnt channels");
    pcnt_chan_config_t chan_a_config = {
        .edge_gpio_num = gpio_enca,
        .level_gpio_num = gpio_encb,
    };
    pcnt_channel_handle_t pcnt_chan_a = NULL;
    ESP_ERROR_CHECK(pcnt_new_channel(pcnt_unit, &chan_a_config, &pcnt_chan_a));
    pcnt_chan_config_t chan_b_config = {
        .edge_gpio_num = gpio_encb,
        .level_gpio_num = gpio_enca,
    };
    pcnt_channel_handle_t pcnt_chan_b = NULL;
    ESP_ERROR_CHECK(pcnt_new_channel(pcnt_unit, &chan_b_config, &pcnt_chan_b));

    ESP_LOGI(TAG, "set edge and level actions for pcnt channels");
    ESP_ERROR_CHECK(pcnt_channel_set_edge_action(pcnt_chan_a, PCNT_CHANNEL_EDGE_ACTION_DECREASE, PCNT_CHANNEL_EDGE_ACTION_INCREASE));
    ESP_ERROR_CHECK(pcnt_channel_set_level_action(pcnt_chan_a, PCNT_CHANNEL_LEVEL_ACTION_KEEP, PCNT_CHANNEL_LEVEL_ACTION_INVERSE));
    ESP_ERROR_CHECK(pcnt_channel_set_edge_action(pcnt_chan_b, PCNT_CHANNEL_EDGE_ACTION_INCREASE, PCNT_CHANNEL_EDGE_ACTION_DECREASE));
    ESP_ERROR_CHECK(pcnt_channel_set_level_action(pcnt_chan_b, PCNT_CHANNEL_LEVEL_ACTION_KEEP, PCNT_CHANNEL_LEVEL_ACTION_INVERSE));

    ESP_LOGI(TAG, "add watch points and register callbacks");
    int watch_points[] = {unit_config.low_limit, unit_config.high_limit};
    for (size_t i = 0; i < sizeof(watch_points) / sizeof(watch_points[0]); i++) {
        ESP_ERROR_CHECK(pcnt_unit_add_watch_point(pcnt_unit, watch_points[i]));
    }

    ESP_ERROR_CHECK(pcnt_unit_enable(pcnt_unit));
    ESP_ERROR_CHECK(pcnt_unit_clear_count(pcnt_unit));
    ESP_ERROR_CHECK(pcnt_unit_start(pcnt_unit));
    counts_per_rev = cpr;
    return 0;
}

float EncoderSensor::get_position()
{
    return current_revolutions;
}
float EncoderSensor::get_velocity()
{
    return cur_velocity;
}

void EncoderSensor::update_velocity(float dt)
{
    int pulse_count;
    pcnt_unit_get_count(pcnt_unit, &pulse_count);
    current_revolutions = (float)pulse_count / counts_per_rev;
    cur_velocity = (current_revolutions - last_revolutions) / dt;
    last_revolutions = current_revolutions;
}

void EncoderSensor::clear_position()
{
    pcnt_unit_clear_count(pcnt_unit);
}

/* ======================================================= */

bool IMUMotSensor::init(IMUBase *_imu)
{
    imu = _imu;
    return 0;
}

float IMUMotSensor::get_position()
{
    return current_revolutions;
}
float IMUMotSensor::get_velocity()
{
    return cur_velocity;
}

void IMUMotSensor::update_velocity(float dt)
{
    const imu_data_t &data = imu->getData();
    current_revolutions = data.angle.y;
    cur_velocity = data.gyro.y;
}

void IMUMotSensor::clear_position()
{
}

/* Warning:
 * For ESP32, ESP32S2, ESP32S3, ESP32C3, ESP32C2, ESP32C6, ESP32H2, ESP32P4 targets,
 * when LEDC_DUTY_RES selects the maximum duty resolution (i.e. value equal to SOC_LEDC_TIMER_BIT_WIDTH),
 * 100% duty cycle is not reachable (duty cannot be set to (2 ** SOC_LEDC_TIMER_BIT_WIDTH)).
 */
static int g_pwm_count = 0;
bool PWM::init(int pin1, int pin2, int freq_hz)
{
#define LEDC_TIMER              LEDC_TIMER_0
#define LEDC_MODE               LEDC_LOW_SPEED_MODE
#define LEDC_DUTY_RES           LEDC_TIMER_10_BIT

    mot_id = g_pwm_count++;

    ESP_LOGI(TAG, "Initializing motor...");
    // Prepare and then apply the LEDC PWM timer configuration
    ledc_timer_config_t ledc_timer = {
        .speed_mode       = LEDC_MODE,
        .duty_resolution  = LEDC_DUTY_RES,
        .timer_num        = LEDC_TIMER,
        .freq_hz          = (uint32_t)freq_hz,
        .clk_cfg          = LEDC_AUTO_CLK,
        .deconfigure      = false,
    };
    ESP_ERROR_CHECK(ledc_timer_config(&ledc_timer));

    // Prepare and then apply the LEDC PWM channel configuration
    ledc_channel_config_t ledc_channel = {
        .gpio_num       = 0,
        .speed_mode     = LEDC_MODE,
        .channel        = LEDC_CHANNEL_0,
        .intr_type      = LEDC_INTR_DISABLE,
        .timer_sel      = LEDC_TIMER,
        .duty           = 0, // Set duty to 0%
        .hpoint         = 0,
        .sleep_mode     = LEDC_SLEEP_MODE_NO_ALIVE_NO_PD,
        .flags          = {
            .output_invert = 0,
        },
    };

    int channel = LEDC_CHANNEL_0 + mot_id * 2;

    ledc_channel.channel = (ledc_channel_t)channel;
    ledc_channel.gpio_num = pin1;
    ESP_ERROR_CHECK(ledc_channel_config(&ledc_channel));
    ledc_channel.channel = (ledc_channel_t)(channel + 1);
    ledc_channel.gpio_num = pin2;
    ESP_ERROR_CHECK(ledc_channel_config(&ledc_channel));
    return 0;
}

/**
 * @brief Set motor PWM
 * @note
 * @param percent PWM duty cycle, range from -1000 to 1000, 1000 means 100% duty cycle, miuns means reverse direction
 */
void PWM::set_pwm(int32_t percent)
{
    percent = percent > 1000 ? 1000 : percent;
    percent = percent < -1000 ? -1000 : percent;
    int32_t duty = percent * 1024 / 1000;
    int channel = LEDC_CHANNEL_0 + this->mot_id * 2;
    if (percent < 0) {
        ledc_set_duty(LEDC_MODE, (ledc_channel_t)channel, 1024 + duty);
        ledc_set_duty(LEDC_MODE, (ledc_channel_t)(channel + 1), 1024);
    } else {
        ledc_set_duty(LEDC_MODE, (ledc_channel_t)channel, 1024);
        ledc_set_duty(LEDC_MODE, (ledc_channel_t)(channel + 1), 1024 - duty);
    }
    ESP_ERROR_CHECK(ledc_update_duty(LEDC_MODE, (ledc_channel_t)channel));
    ESP_ERROR_CHECK(ledc_update_duty(LEDC_MODE, (ledc_channel_t)(channel + 1)));
}

Motor::Motor(const char *name)
{
    state = MOT_STATE_IDLE;
    max_speed = 100;
    stall_cnt = 0;
    this->name = name;
}
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

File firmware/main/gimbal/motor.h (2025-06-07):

/*
   This example code is in the Public Domain (or CC0 licensed, at your option.)

   Unless required by applicable law or agreed to in writing, this
   software is distributed on an "AS IS" BASIS, WITHOUT WARRANTIES OR
   CONDITIONS OF ANY KIND, either express or implied.
*/
#pragma once
#include <stdint.h>
#include "driver/pulse_cnt.h"
#include "pid.h"
#include "imu_base.h"
#include "setting.h"

#define MOT_STATE_LIST \
X(MOT_STATE_IDLE, "Idle") \
X(MOT_STATE_RUNNING, "Running") \
X(MOT_STATE_WARNING, "Warning") \

typedef enum {
#define X(name, desc) name,
    MOT_STATE_LIST
#undef X
    MOT_STATE_COUNT
} mot_state_t;


class PWM {
public:
    PWM() = default;
    ~PWM() = default;

    // 初始化PWM
    bool init(int pin1, int pin2, int freq_hz);

    // 设置PWM占空比
    void set_pwm(int32_t percent);
private:
    int mot_id;
};


class MotorSensor {
public:
    virtual ~MotorSensor() = default;

    // 初始化传感器
    // virtual bool init() = 0;

    // 获取位置（圈数）
    virtual float get_position() = 0;

    // 获取速度（圈/秒）
    virtual float get_velocity() = 0;

    // 清除位置计数
    virtual void clear_position() = 0;

    // 更新速度
    virtual void update_velocity(float dt) = 0;

    // 设置每圈的计数分辨率
    void set_counts_per_rev(float cpr)
    {
        counts_per_rev = cpr;
    }

    // 获取每圈的计数分辨率
    float get_counts_per_rev() const
    {
        return counts_per_rev;
    }

protected:
    float counts_per_rev = 0.0f;  // 每圈计数值
};

class EncoderSensor : public MotorSensor {
public:
    EncoderSensor() {};
    virtual ~EncoderSensor() {};

    bool init(int gpio_enca, int gpio_encb, float cpr);

    float get_position() override;
    float get_velocity() override;
    void clear_position() override;
    void update_velocity(float dt) override;

private:
    pcnt_unit_handle_t pcnt_unit;
    float last_revolutions = 0.0f;
    float cur_velocity = 0.0f;
    float current_revolutions = 0.0f;
};

class IMUMotSensor : public MotorSensor {
public:
    IMUMotSensor() {};
    virtual ~IMUMotSensor() {};

    bool init(IMUBase *_imu);

    float get_position() override;
    float get_velocity() override;
    void clear_position() override;
    void update_velocity(float dt) override;

private:
    IMUBase *imu;
    float cur_velocity = 0.0f;
    float current_revolutions = 0.0f;
};


class Motor {
public:
    Motor(const char *name);
    Motor(const char *name, float gearRatio) : Motor(name)
    {
        this->gearRatio = gearRatio;
    }

    // 禁止拷贝构造和赋值操作
    Motor(const Motor &) = delete;
    Motor &operator=(const Motor &) = delete;

    void attach_sensor(MotorSensor *sensor);
    void attach_driver(PWM *pwm);

    void run(float dt); // 运行电机，周期调用
    void enable(bool is_enable);
    void set_position(float position)
    {
        this->target_position = position * gearRatio / 360.0f;
    }

    float get_position() 
    {
        return this->sensor->get_position() * 360.0f / gearRatio;
    }
    void set_max_speed(float max_speed)
    {
        this->max_speed = max_speed;
    }
    float get_max_speed()
    {
        return this->max_speed;
    }
    mot_state_t get_state()
    {
        return this->state;
    }
    const char *get_state_description() const
    {
        return motStateDescriptions[state];
    }

    float get_velocity()
    {
        return this->sensor->get_velocity();
    }
    void clear_position()
    {
        this->sensor->clear_position();
    }

    struct pid positionPID;
    struct pid velocityPID;
private:
    static const char *motStateDescriptions[];
    const char *name;
    MotorSensor *sensor;
    PWM *pwm;
    float target_speed;
    float target_position;
    uint32_t stall_cnt = 0;
    mot_state_t state; // 电机状态
    float max_speed; // 最大速度
    float gearRatio = 1.0f; // 齿轮比, default 1

};

#ifdef __cplusplus
extern "C" {
#endif


#ifdef __cplusplus
}
#endif

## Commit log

2025-03-03 fw: add web server
    [partitions_4mb_optimised.csv]
2025-03-04 fw: update webserver
    [partitions_4mb_optimised.csv]
2025-03-06 front: add pid parameter card
2025-03-10 fw: temp
    [partitions_4mb_optimised.csv]
2025-03-16 fw: add bmi270 and remove wit imu
2025-03-27 fw: update for motor
2025-03-31 fw: refactor motor
2025-03-31 hw: update
    [BOM-solar_tracer.csv, Power.kicad_sch, imu.kicad_sch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]
2025-04-07 add 3d
    [2814300907JGY-370编码器.STEP, imu固定板.SLDPRT, imu固定板.STEP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]
2025-06-02 add ota web
    [partitions.csv]
2025-06-10 3d: update
    [SS_01GL_E.step, U型板.SLDPRT, U型板.STEP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]
